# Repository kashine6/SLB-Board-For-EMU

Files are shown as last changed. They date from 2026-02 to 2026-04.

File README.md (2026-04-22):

# SLB-Board-For-EMU

**The mass-produced boards is now available on AliExpress.**

 [Aliexpress](https://www.aliexpress.com//item/1005012025112049.html)

**⚠️ WARNING ⚠️**

Incorrect operations such as reversing the 24V/GND 🔌 or causing a short circuit ⚡ may damage the board. Since EMU uses multiple boards in series 🔗, please carefully ensure that all wiring is correct ☑️.

## Table of Contents

- [Introduction](#introduction)
- [1. PIN Diagram](#1-pin-diagram)
- [2. EMU Wiring Diagram](#2-emu-wiring-diagram)
- [3. EMU Configuration](#3-emu-configuration)
- [4. User Guide for EMU](#4-user-guide-for-emu)
- [5. Flashing Guide (Optional)](#5-flashing-guide-optional)
  - [5.1. Flashing Katapult (Optional)](#51-flashing-katapult-optional)
  - [5.2. Compiling Klipper Firmware](#52-compiling-klipper-firmware)
  - [5.3. Updating Firmware via Katapult](#53-updating-firmware-via-katapult)
  - [5.4. Updating Firmware via DFU](#54-updating-firmware-via-dfu)

---

## Introduction
**SLB (Solo Lane Board)** is a control board designed specifically for **EMU**-style MMU systems, where each lane is driven by an independent controller board.  

No WAGO connectors and no LED daisy-chaining. Supports power and CANBUS cascading, and is compatible with the EMU_Hatch_Board, greatly simplifying EMU wiring.

**Notice:** Maximum rated current for SLB is 8A. If you plan to use PTC drying, only one unit can be operated at a time. For more than one unit, please use WAGO terminals to connect the power supply in parallel.

The SLB is not only suitable for EMU, but can also provide additional channel expansion for systems such as BoxTurtle. The board itself includes built-in support for controlling N20 motors.

This board is factory-produced using high-quality electronic components with SMT assembly, ensuring reliable and consistent quality.

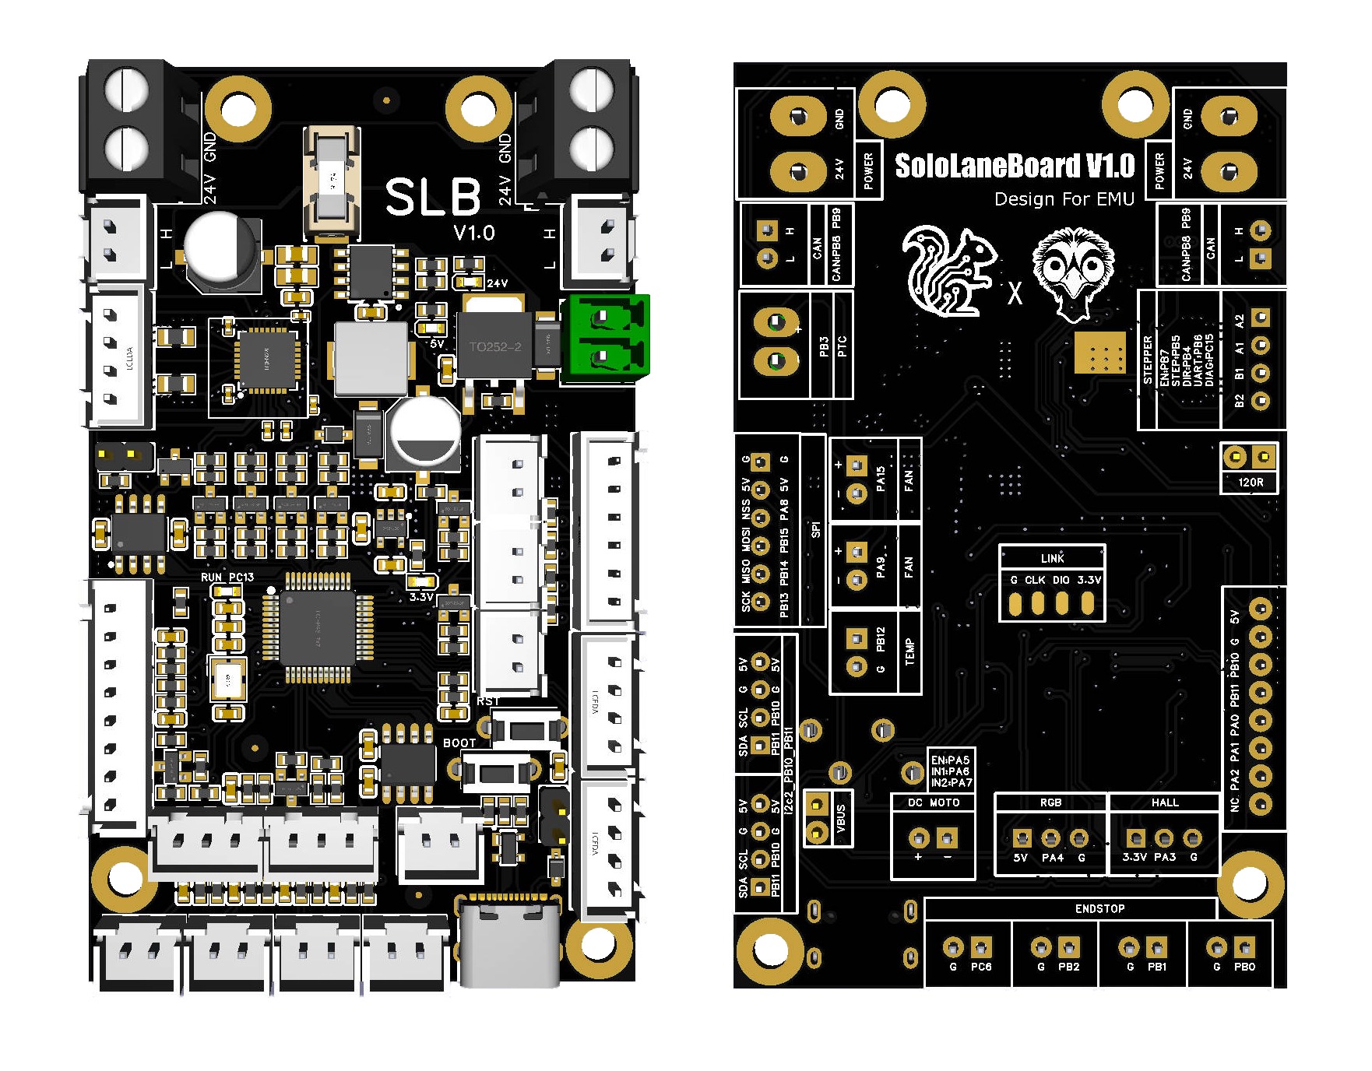
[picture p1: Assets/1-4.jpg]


**It has the following features:**

- **Main Chip**: STM32G0B1CBT6 MCU.
- **Dual power connectors and dual CAN interfaces** for convenient daisy-chaining.
- **1 x Onboard TMC2209** operating in UART mode, with 5V logic circuitry.
- **1x 8-pin XH2.54 connector** is provided for direct connection to the **EMU Hatch Board**.
- **2 × Neo pixel RGB interfaces**, one of which is integrated into the 8-pin XH2.54 connector.
- **6 × I/O connectors**, two of which are integrated into the 8-pin XH2.54 connector.
- **3 × Hardware I2C interfaces**, one of which is integrated into the 8-pin XH2.54 connector.
- **2 × 24V fans** with adjustable speed control
- **1 × PTC heating interface**, 5A max
- **1 × NTC temperature sensor** interface for temperature monitoring
- **1 x Hall ADC interfaces** for PSF Sensor
- **1 x 5V Brushed DC motor drivers** with forward/reverse support, En pin, and sleep mode, support hardware PWM.
- **1 x Hardware SPI interfaces**

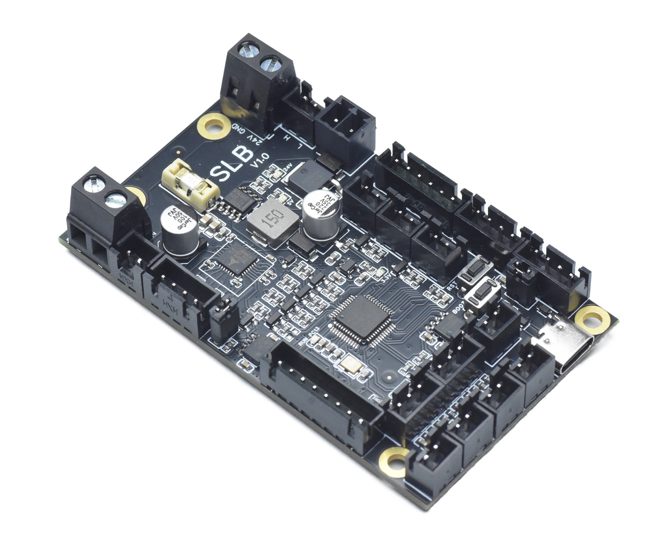
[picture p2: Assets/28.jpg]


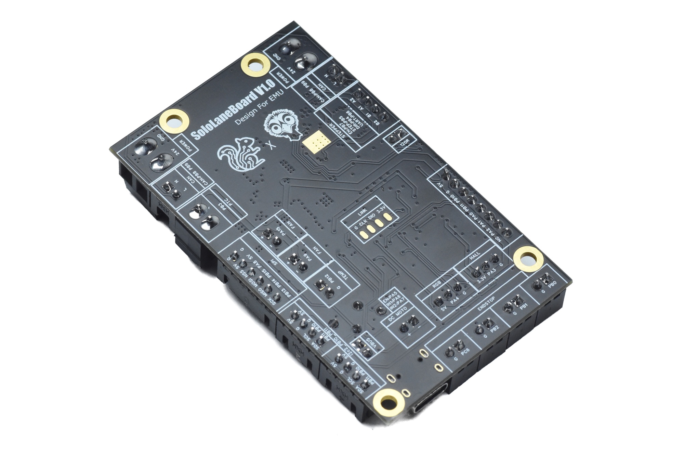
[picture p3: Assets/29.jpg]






## 1. PIN Diagram

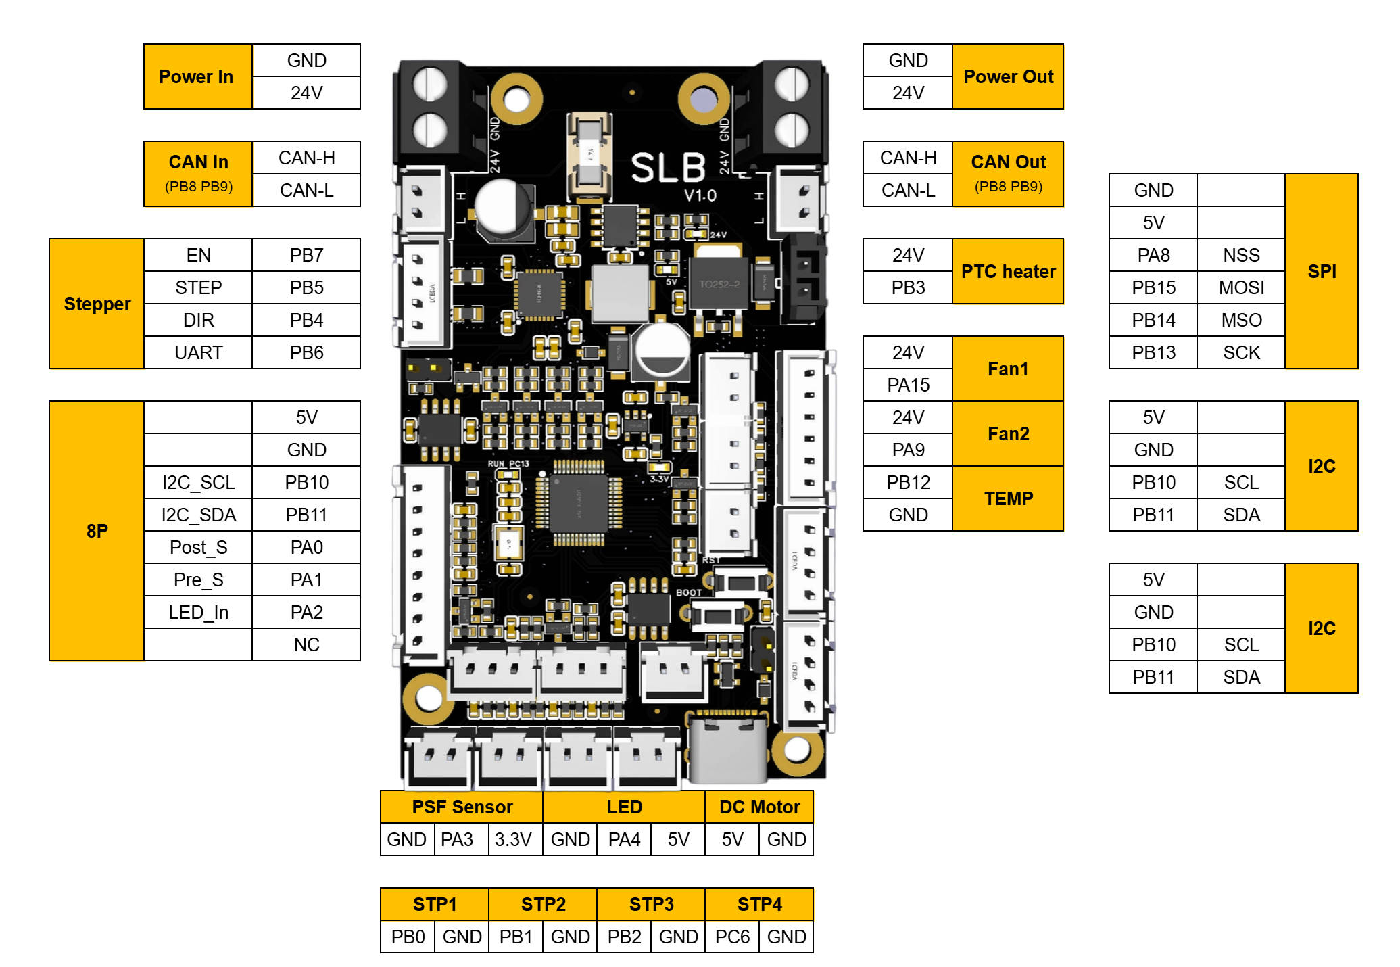
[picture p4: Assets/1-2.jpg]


## 2. EMU Wiring Diagram

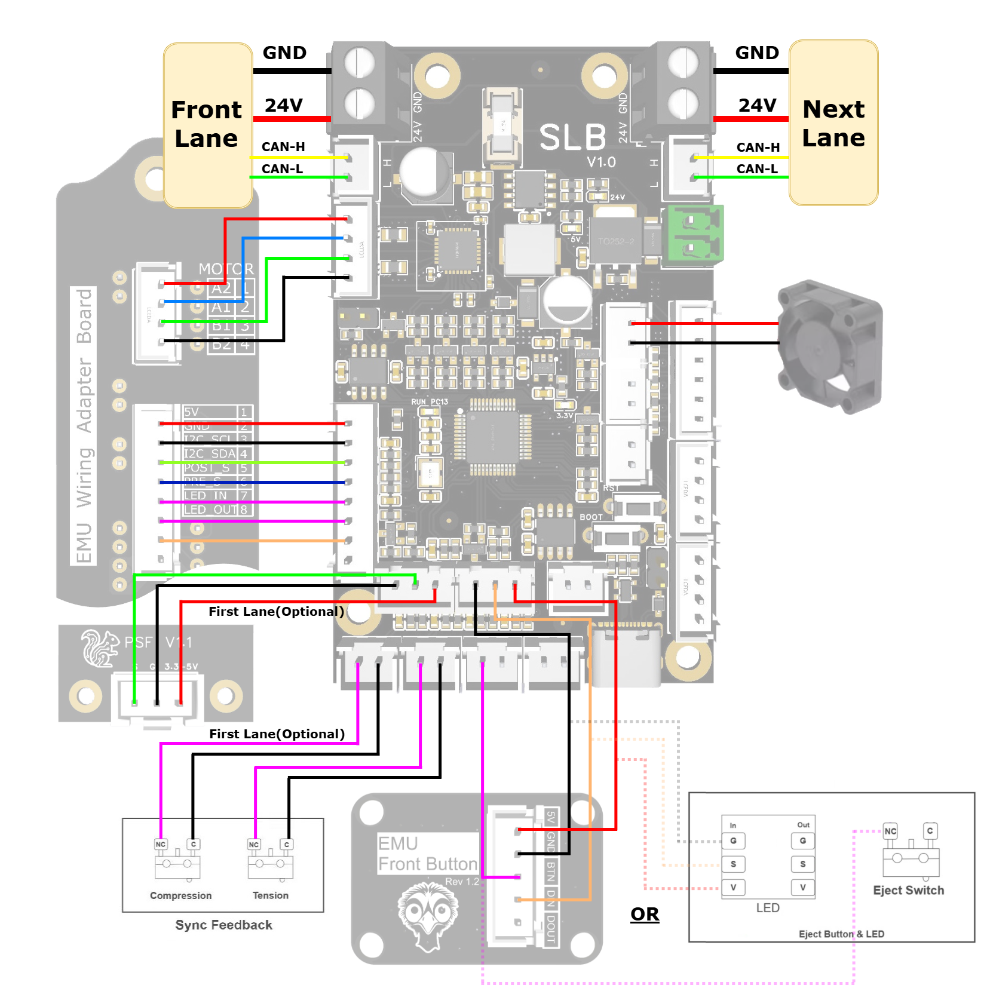
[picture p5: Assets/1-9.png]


For detailed wiring information, please refer to the official EMU documentation:

https://github.com/DW-Tas/EMU/tree/main/docs/assembly_wiring/#solo-lane-board-slb-wiring-dimensions

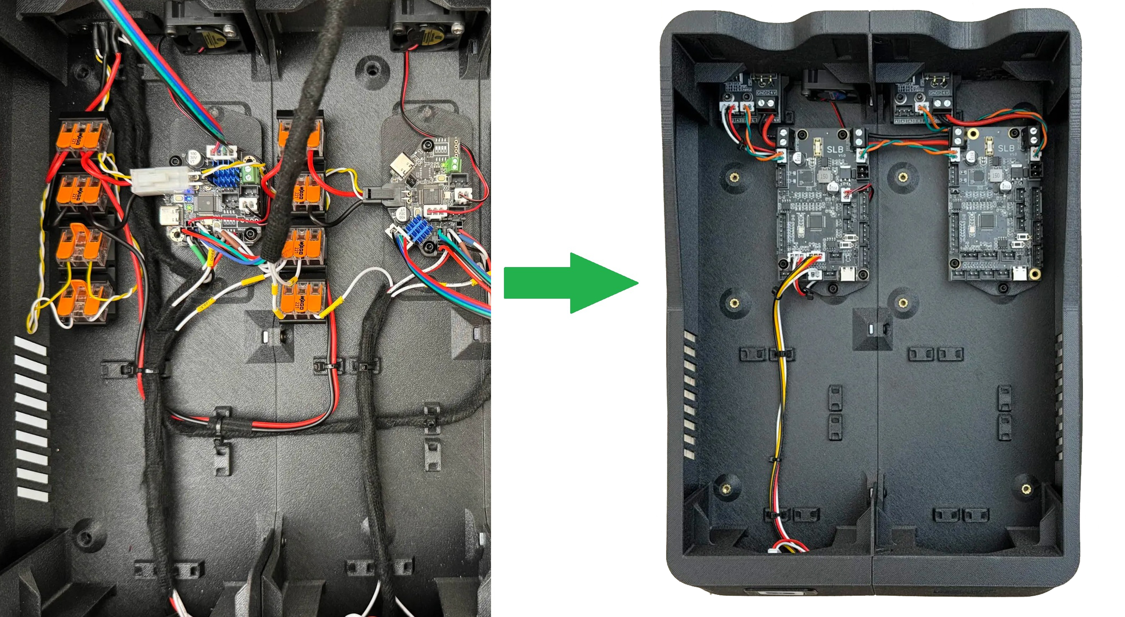
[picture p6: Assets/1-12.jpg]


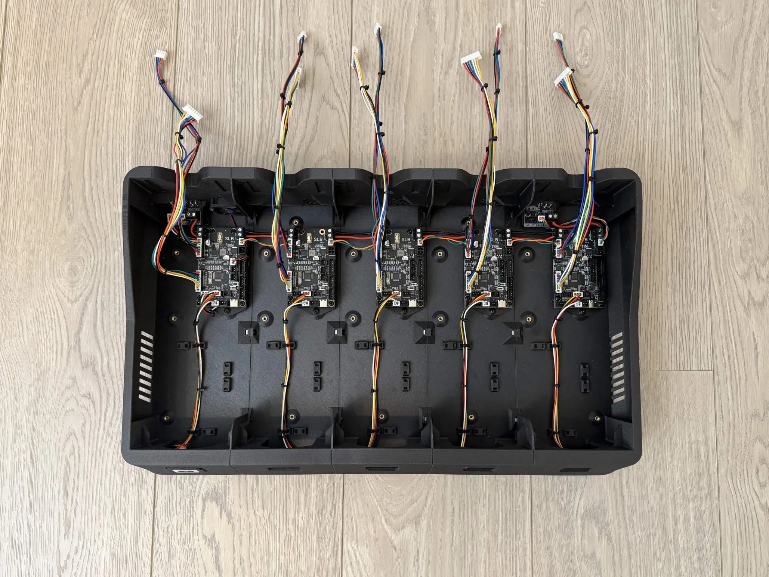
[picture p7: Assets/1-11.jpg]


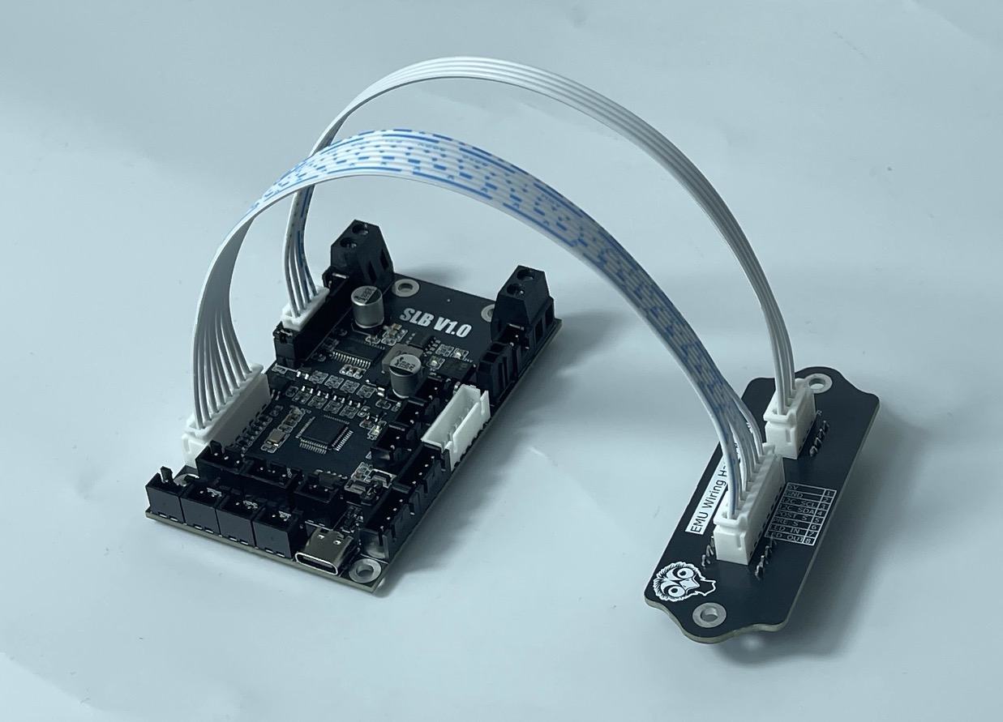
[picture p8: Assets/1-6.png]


**Note:** The wiring harness is for demonstration purposes only. Standard ribbon cables are relatively stiff; you may use silicone ribbon cables or regular loose wires instead.

## 3. EMU Configuration

Please refer to the official EMU documentation:

https://github.com/DW-Tas/EMU/blob/main/docs/software_setup/02-happy-hare-setup.md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

## 4. User Guide for EMU

🟦Has the firmware been flashed

> The **Katapult + Klipper** firmware has already been flashed before shipping, and the CANBUS speed is 1,000,000. So in normal cases, there is no need to reflash.  

🟦About How to use

> You can mount it directly onto the EMU. Note that you may need to remove most of the `120Ω jumpers` on the SLB board (usually keeping only the last one). When the system is unpowered, make sure to use a multimeter to measure the resistance between CAN-H and CAN-L, which should be 60Ω.

🟦How to find the UUID

>Start from the first lane (lane0). Double-click the reset button, then use the command below to find all UUIDs. The UUID shown as “canboot” is the UUID of the current lane. Press the reset button once again; at this point, you will find that the UUID marked as “canboot” is no longer displayed. Then continue the same procedure for the next lane.

``` 
~/klippy-env/bin/python ~/klipper/scripts/canbus_query.py can0
```

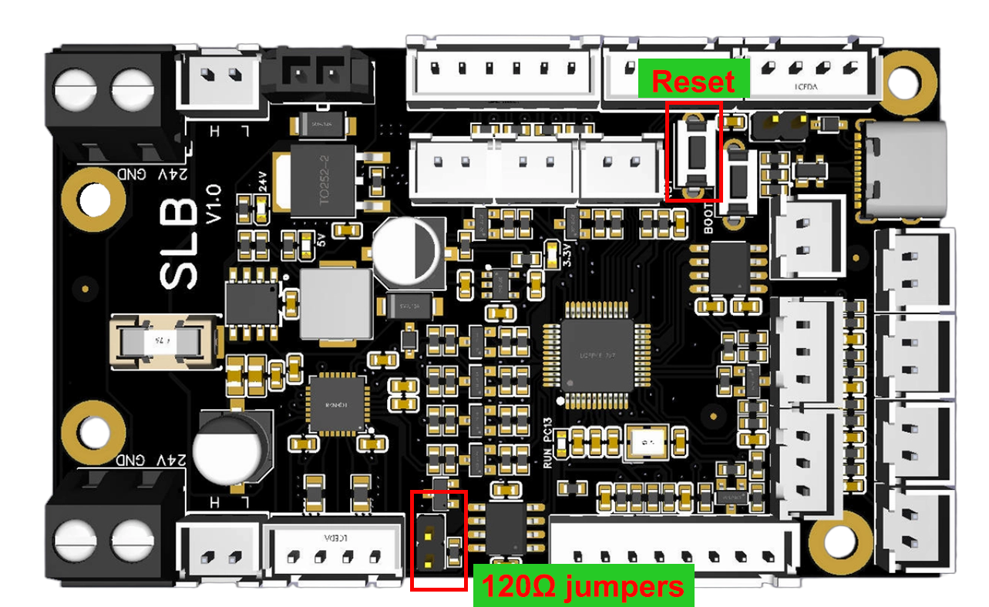
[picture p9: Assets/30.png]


## 5. Flashing Guide (Optional)

> [!TIP]  
>
> The **Katapult + Klipper** firmware has already been flashed before shipping, and the CANBUS speed is 1,000,000. So in normal cases, there is no need to reflash.  
>
> If it is really necessary, you can directly refer to **section 5.3** to upgrade the Klipper firmware using Katapult.

### 5.1 Flashing Katapult (Optional)

Users who only use a CAN connection and want the convenience of quick firmware updates by pressing the Reset button can choose to flash Katapult (formerly known as Canboot).

Katapult is not mandatory, regardless of whether you use a CAN or USB connection.

```bash
# Go to the home directory
cd ~
 
# Download katapult (skip if you already have it)
git clone https://github.com/Arksine/katapult
 
# Enter the katapult directory
cd katapult
```

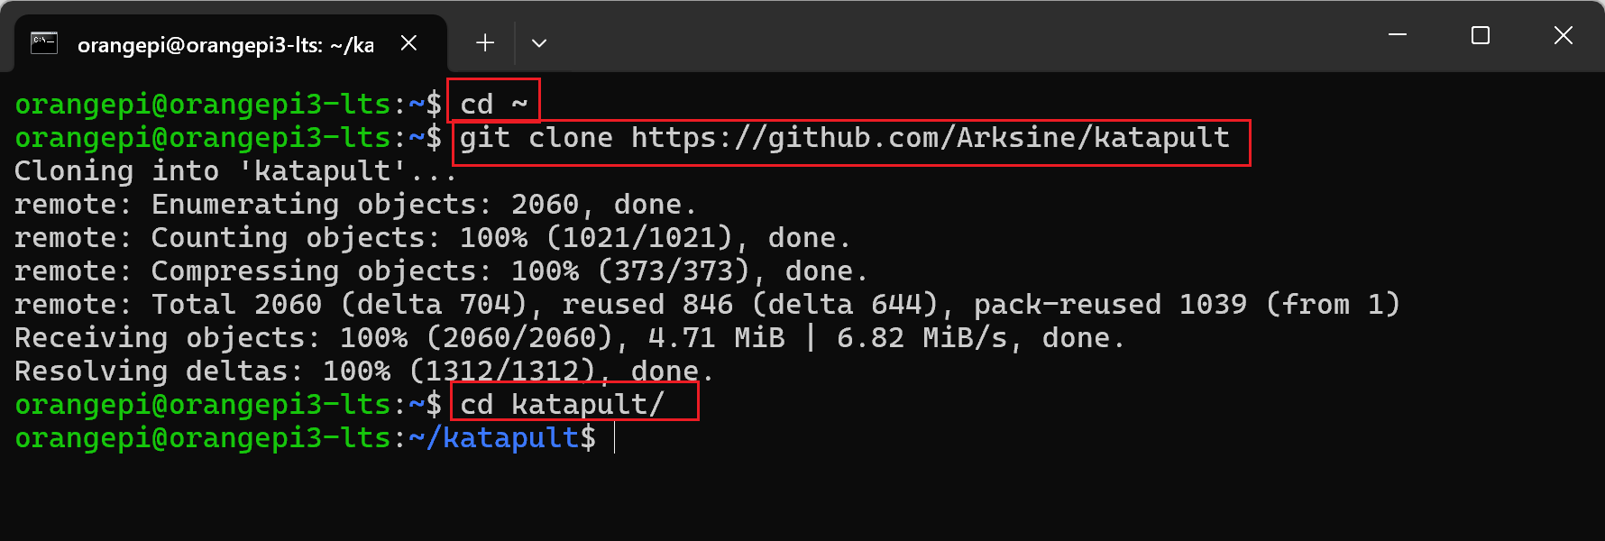
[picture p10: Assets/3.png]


```bash
# Clean the previous build
make clean
 
# Modify the build configuration, fill in the parameters as shown in the image below
make menuconfig
 
# After verifying the settings, press q to exit, select y, then type make to start compiling
make
```

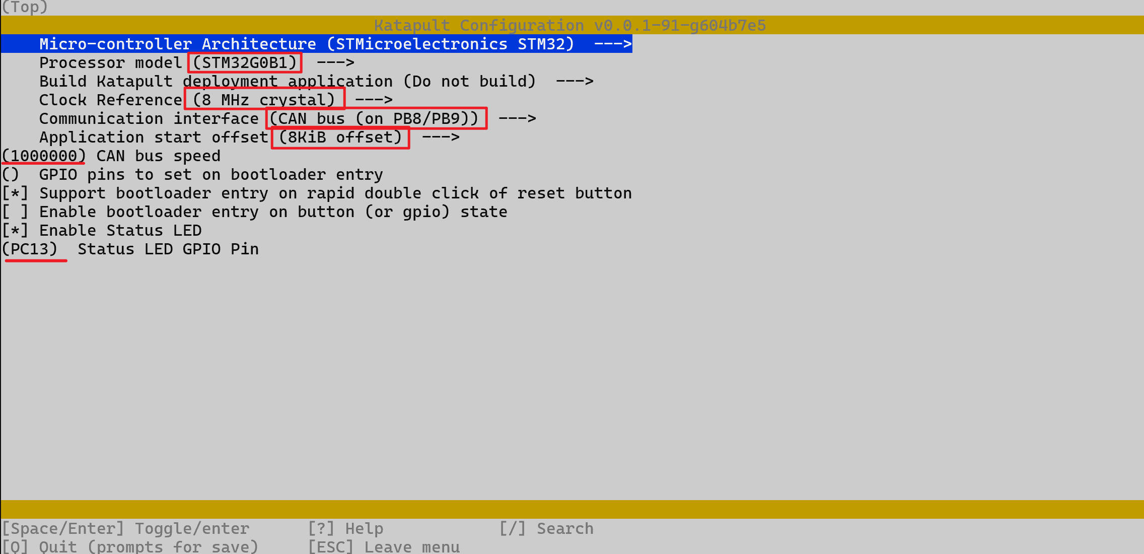
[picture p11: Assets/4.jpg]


> [!TIP]
> The speed can be set according to your needs, 1000000 is recommended.

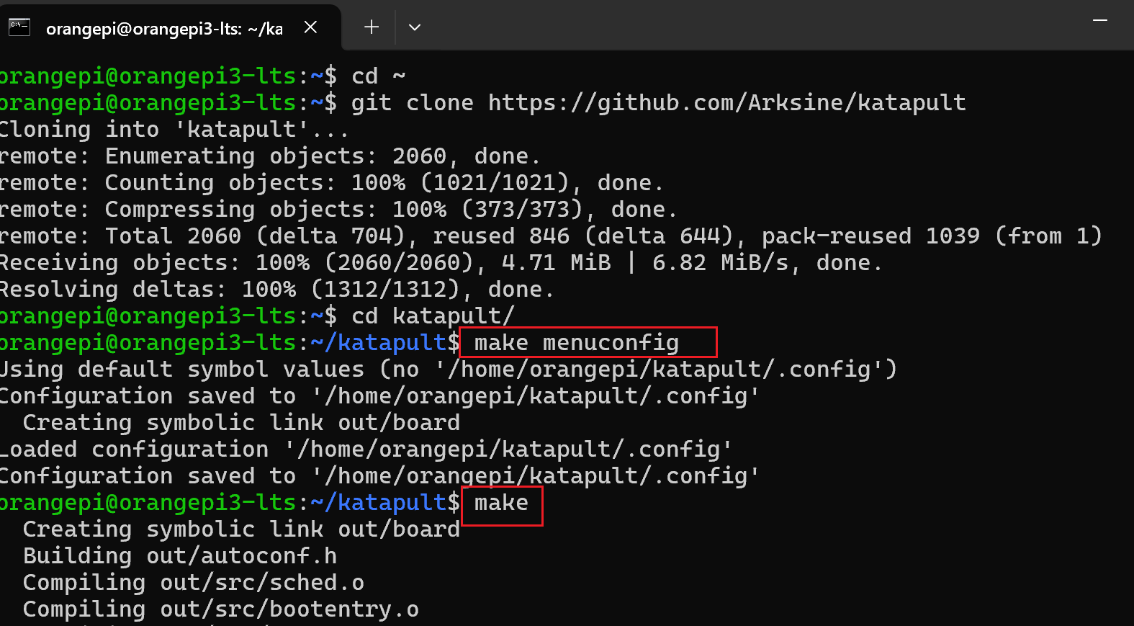
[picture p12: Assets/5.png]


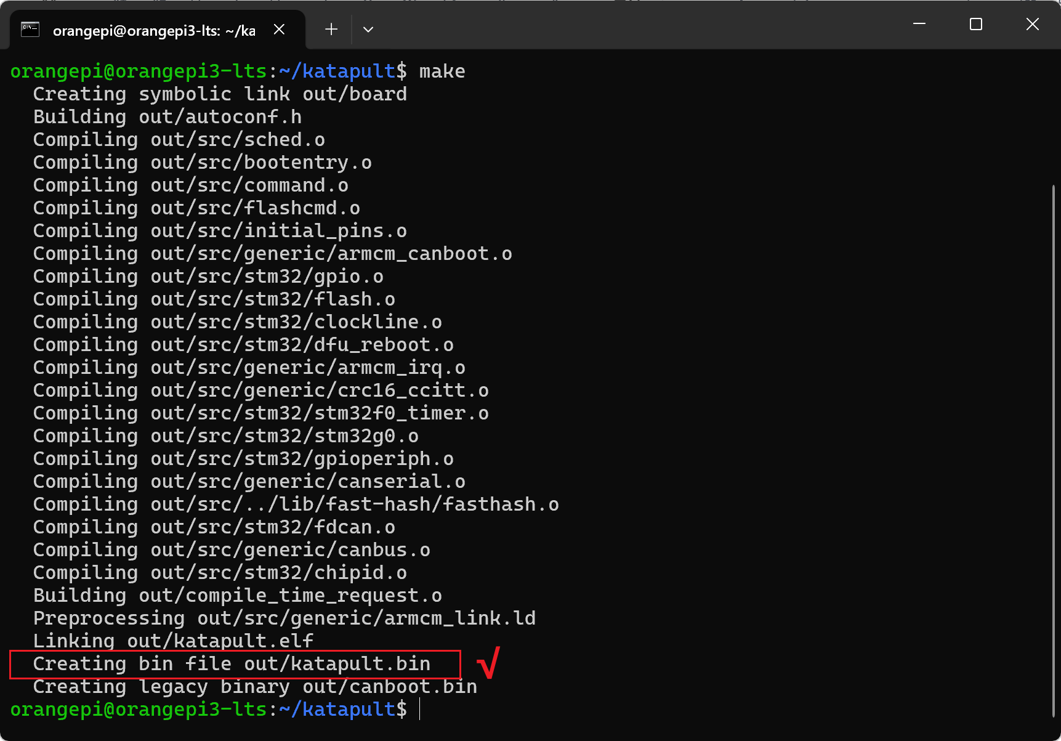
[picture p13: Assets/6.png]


After compilation, katapult.bin will be generated in the ~/katapult/out folder.

**Entering DFU Mode**

Use a jumper to short the 5V USB pins. After shorting, you can power the board via USB for flashing. 

> [!TIP]
> Remember to remove the jumper after flashing is complete.  

If you are using 24V to power the board, you do not need to short the jumper, but you can only use Method 2 below to enter DFU mode.

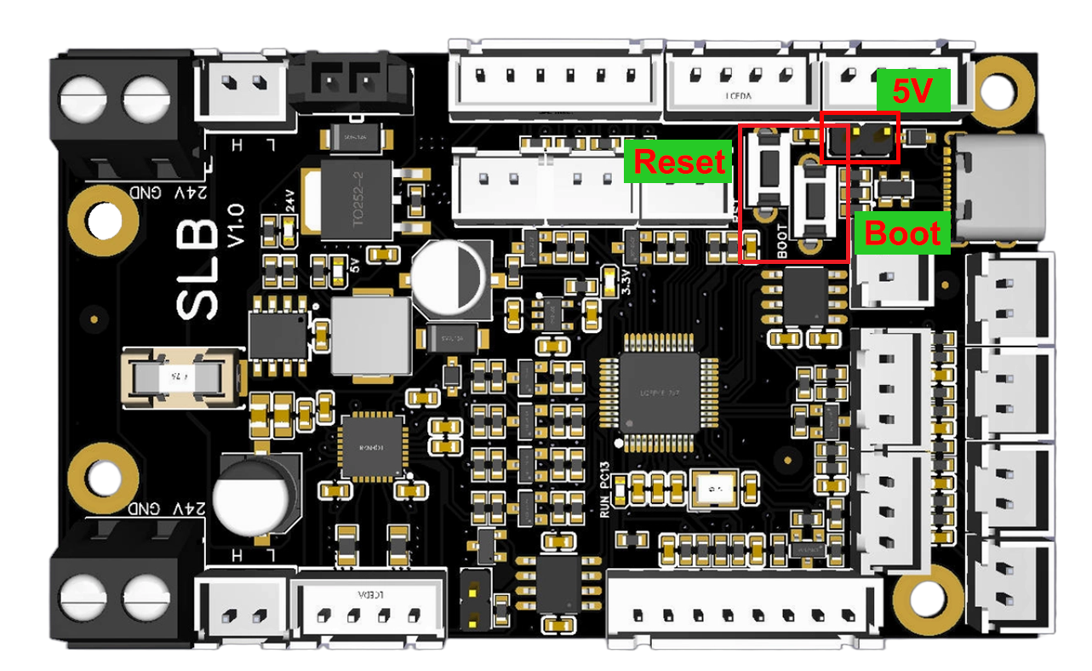
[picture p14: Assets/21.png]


- **Method 1 to enter DFU:** With the board completely powered off, press and hold the Boot button, connect the board to the host computer with a Type-C cable, then release the Boot button.

- **Method 2 to enter DFU:** If the board is powered on, connect it to the host computer with a Type-C cable, then press and hold the Boot button, press and release the Reset button, release the Reset button, and finally release the Boot button.

Then use the lsusb command to check if a DFU device is present.

```bash
lsusb
```

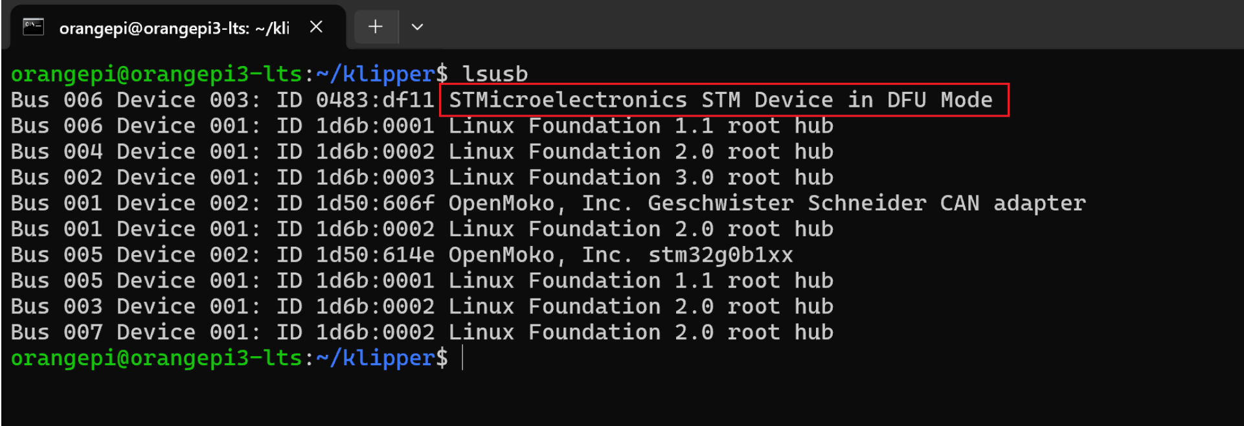
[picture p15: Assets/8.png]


Use the following command to flash the board:

```bash
make flash FLASH_DEVICE=0483:df11
```

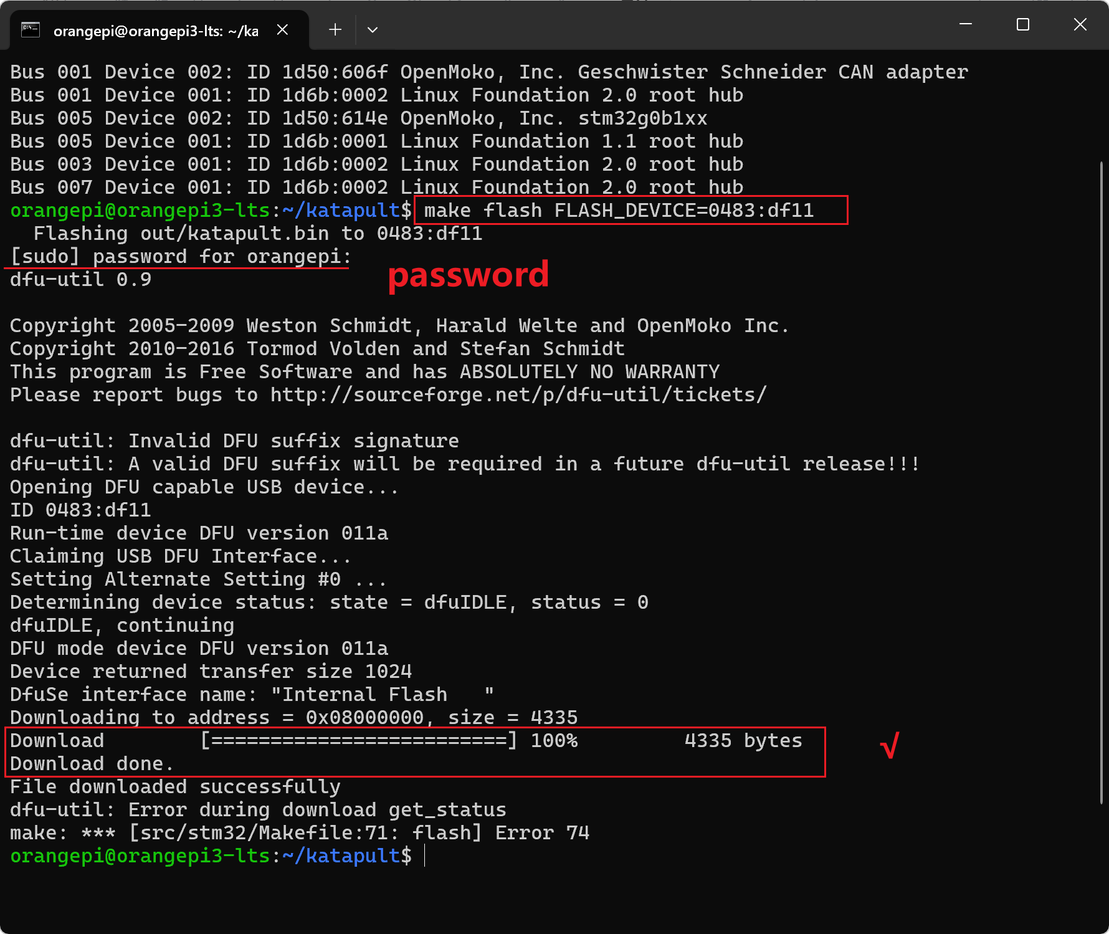
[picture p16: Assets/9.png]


After flashing is complete, please unplug the USB cable and connect the CAN signal cable and 24V power supply.

> [!NOTE]
> 1: Remember to remove the 5V USB jumper.  
> 2: If you have multiple CAN devices, you only need to short the 120-ohm resistor on one device. It is best to short the 120-ohm resistor on the mainboard at the end of the chain.  
> 3: Pay close attention to the wiring order of 24V, GND, CAN-H, and CAN-L. Double-check carefully. Incorrect wiring may cause the mainboard to burn out, and you will be responsible for the consequences.  

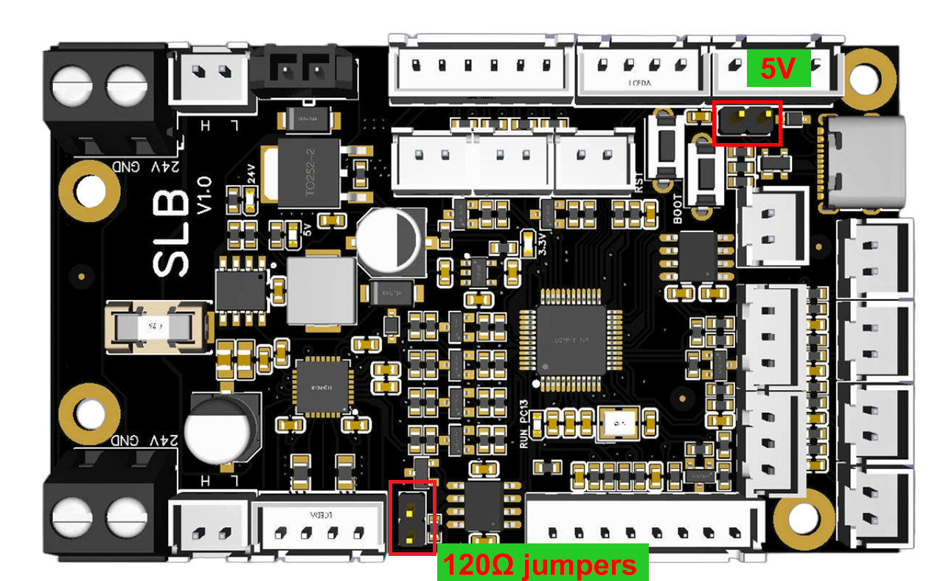
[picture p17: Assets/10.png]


Use the following command to check the CAN UUID. 
> [!TIP]
> You may need to quickly double-press the reset button to enter the bootloader.

```bash
~/klippy-env/bin/python ~/klipper/scripts/canbus_query.py can0
```

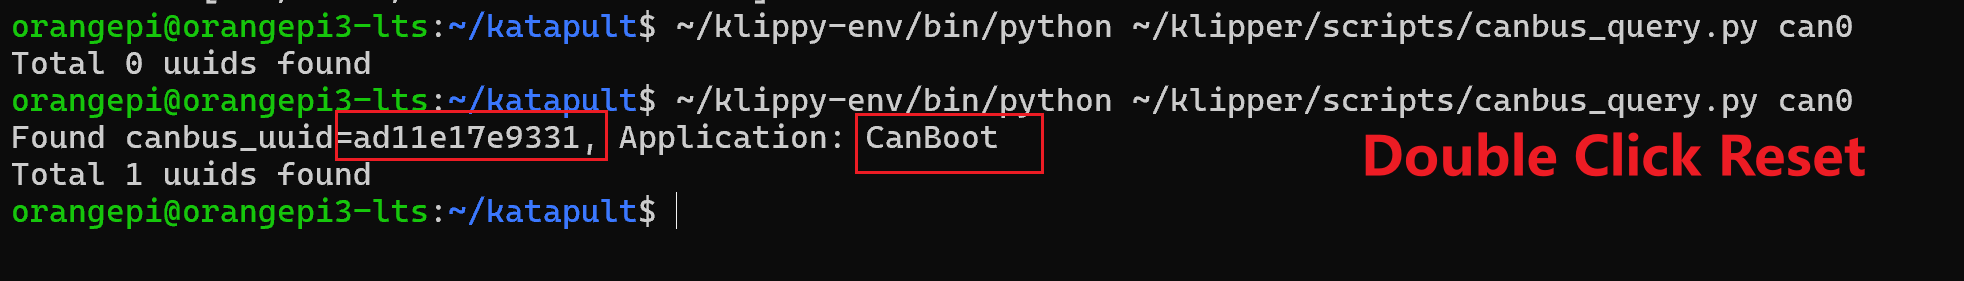
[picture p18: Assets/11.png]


### 5.2 Compiling Klipper Firmware

SSH into your host machine.

```bash
# cd to the klipper directory
cd ~/klipper
 
# Clean the previous build
make clean
 
# Configure the build parameters [refer to the image below]
make menuconfig
```



Set the build parameters according to the protocol you need to use.

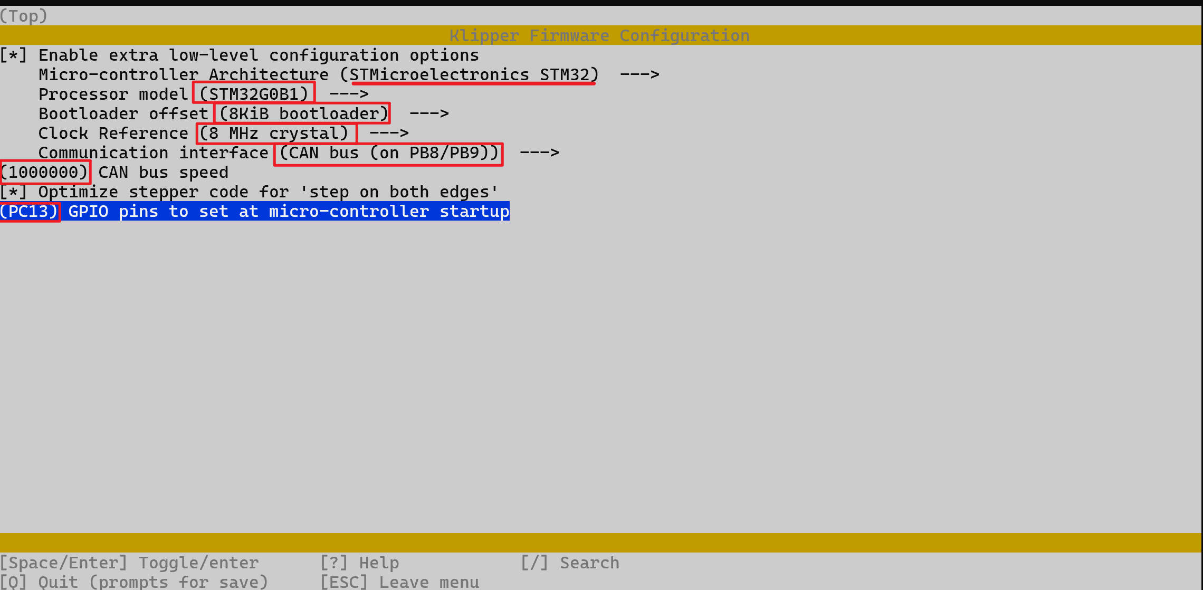
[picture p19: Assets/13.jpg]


```bash
# If not using Katapult
Bootloader offset (No bootloader) --->
 
# If using Katapult
Bootloader offset (8KiB bootloader) --->
 
# If using USB communication via Type-C
Communication interface (USB (on PA11/PA12)) --->
 
# If using CANBus communication
Communication interface (CAN bus (on PB8/PB9)) --->
 (1000000) CAN bus speed
```

Press `q` to exit, and `y` to save.

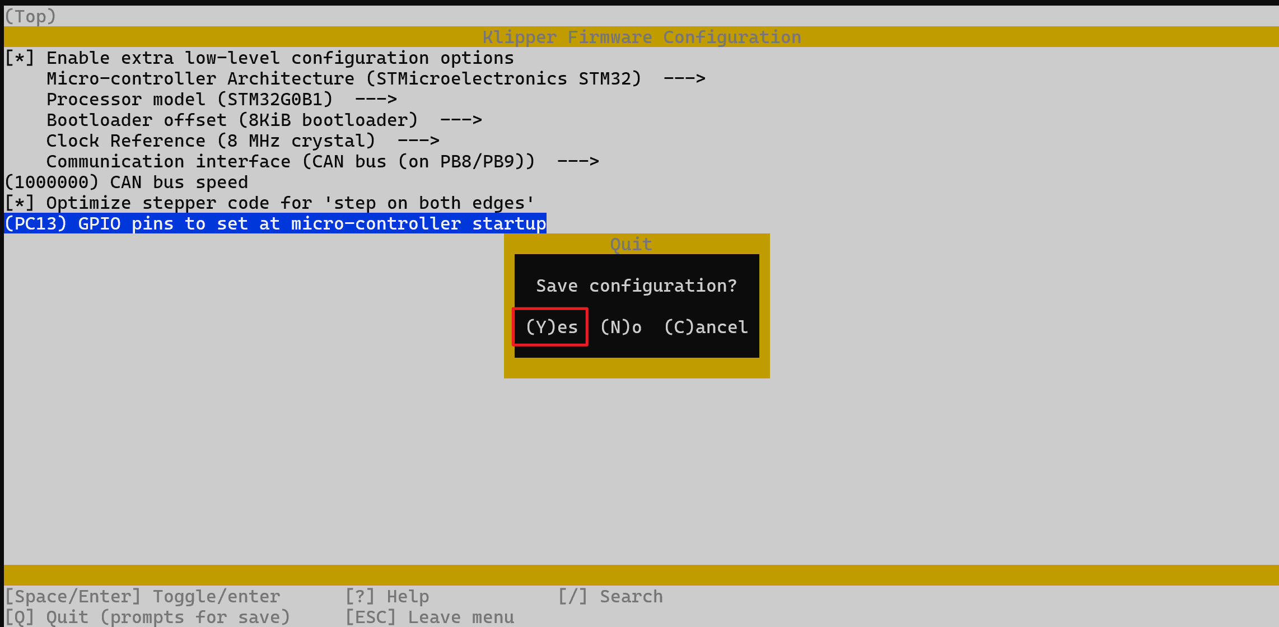
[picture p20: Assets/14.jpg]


Enter the make command to start compiling.

```bash
make
```

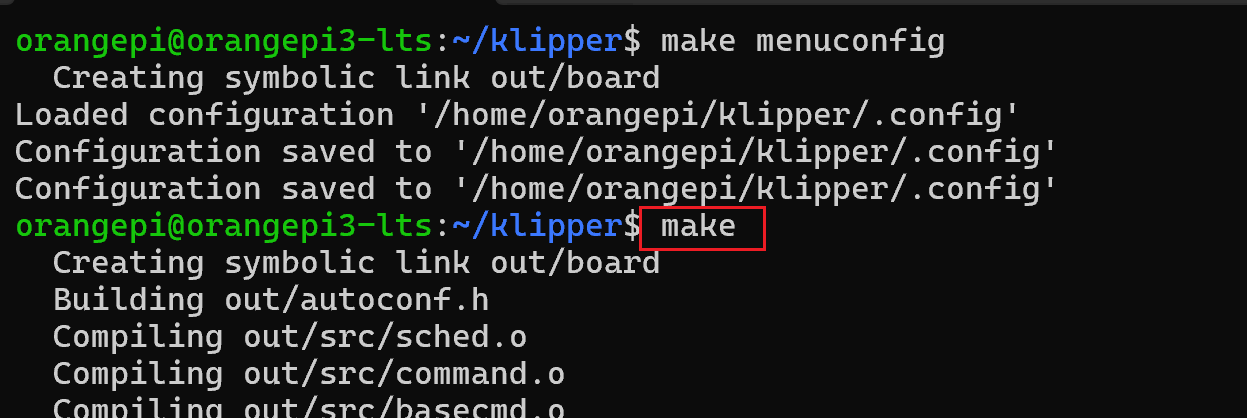
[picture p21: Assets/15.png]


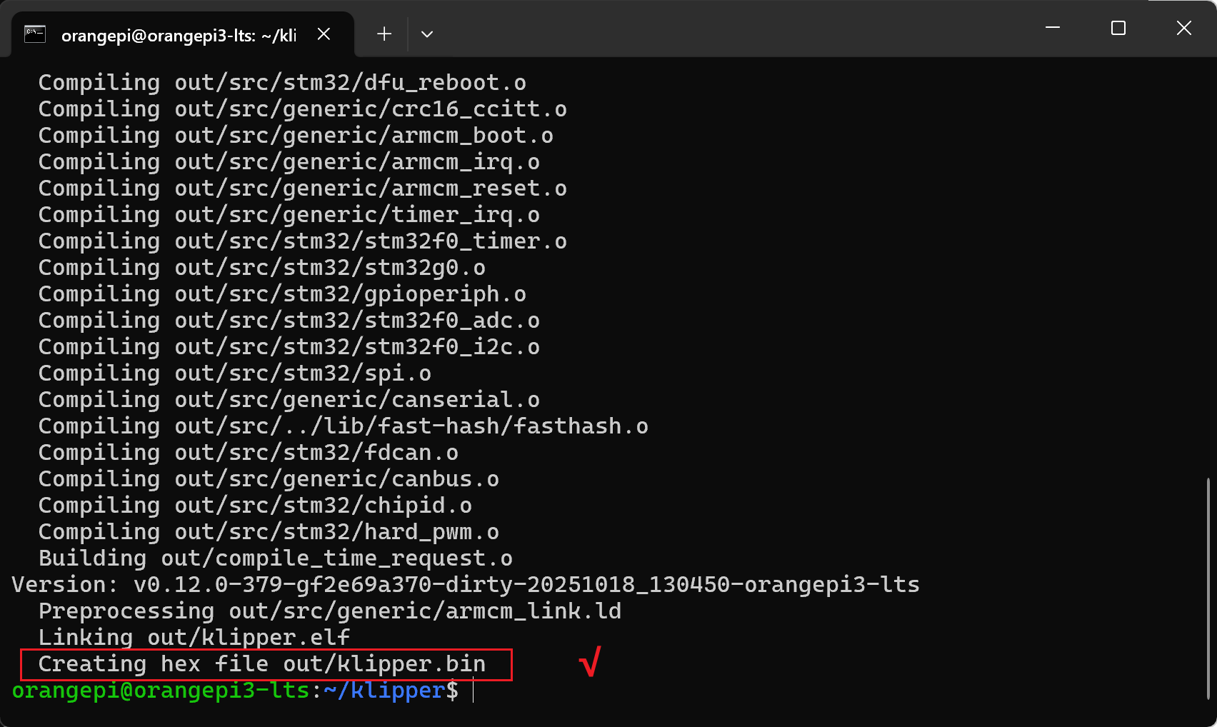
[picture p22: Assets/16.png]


### 5.3 Updating Firmware via Katapult

Connect the CAN signal cable and 24V power supply.

> [!NOTE]
> 1: Remember to remove the 5V USB jumper.  
> 2: If you have multiple CAN devices, you only need to short the 120-ohm resistor on one device.  
> 3: Pay close attention to the wiring order of 24V, GND, CAN-H, and CAN-L. Double-check carefully. Incorrect wiring may cause the mainboard to burn out, and you will be responsible for the consequences.  



Then use the following command to check the UUID:

```bash
~/klippy-env/bin/python ~/klipper/scripts/canbus_query.py can0
```

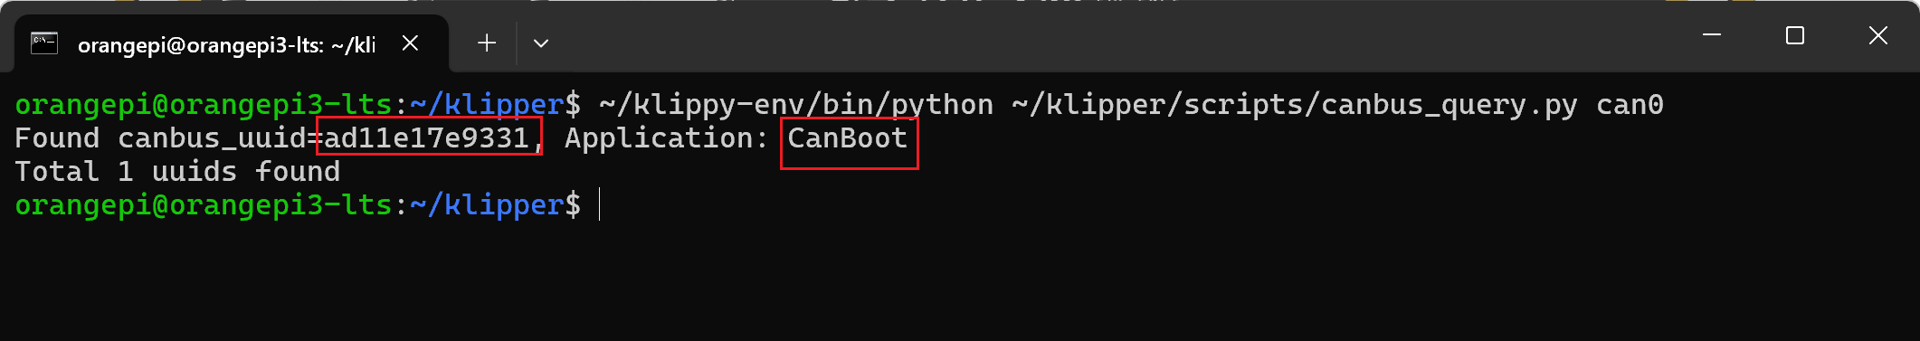
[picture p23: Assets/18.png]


Use the following command to flash in CAN mode:

```bash
cd ~/katapult/scripts
 
python3 flashtool.py -i can0 -f ~/klipper/out/klipper.bin -u your_uuid_here
```

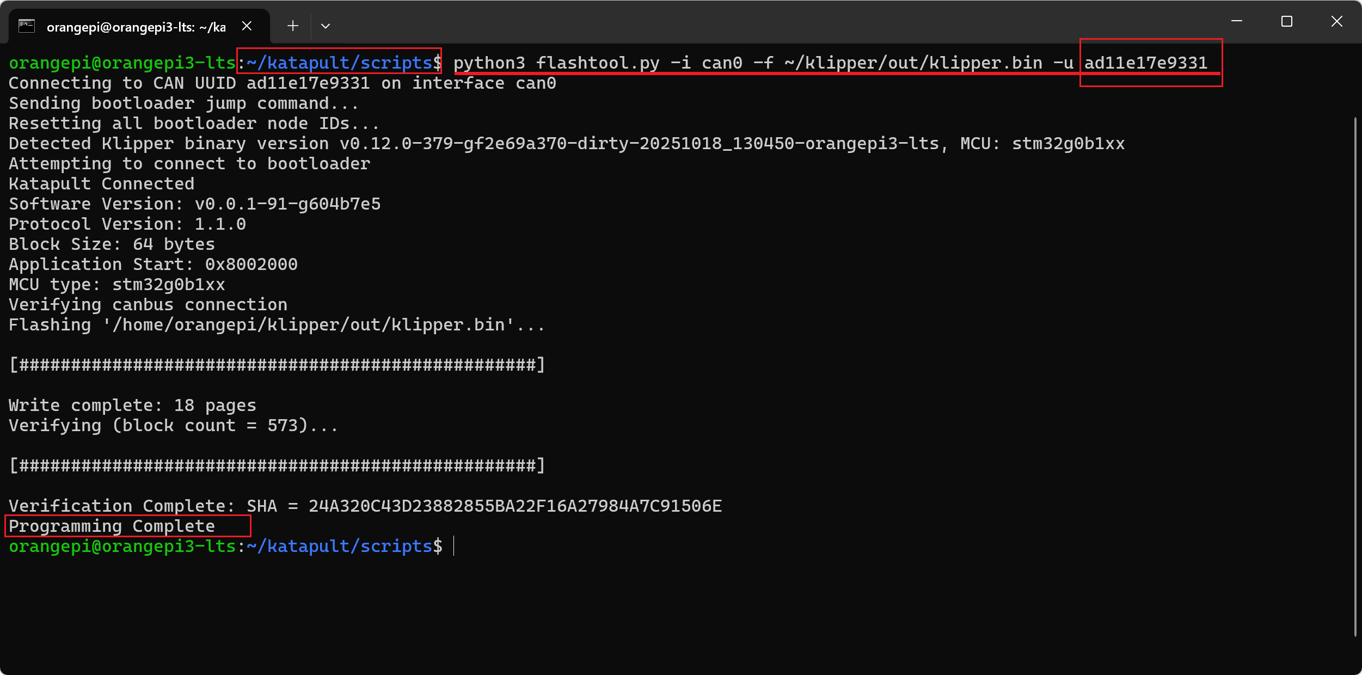
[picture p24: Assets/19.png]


Then continue to use the previous command to check the CAN information.



> [!TIP]
> To upgrade the CAN firmware in the future, repeat this process. When compiling the Katapult firmware earlier, we set it to enter Katapult mode by double-pressing the reset button. 
> In practice, you can also directly enter the flashing command, and the board will automatically restart and enter Katapult.  

### 5.4 Updating Firmware via DFU

1: Enter DFU mode.

Use a jumper to short the 5V USB pins. After shorting, you can power the board via USB for flashing. 

> [!TIP]
> Remember to remove the jumper after flashing is complete.

If you are using 24V to power the board, you do not need to short the jumper, but you can only use Method 2 below to enter DFU mode.



- Method 1 to enter DFU: With the board completely powered off, press and hold the Boot button, connect the board to the host computer with a Type-C cable, then release the Boot button.

- Method 2 to enter DFU: If the board is powered on, connect it to the host computer with a Type-C cable, then press and hold the Boot button, press and release the Reset button, release the Reset button, and finally release the Boot button.

2: In SSH, type lsusb to check if a DFU device appears. Normally, a DFU device should appear.

If no DFU device appears, repeat the operation.

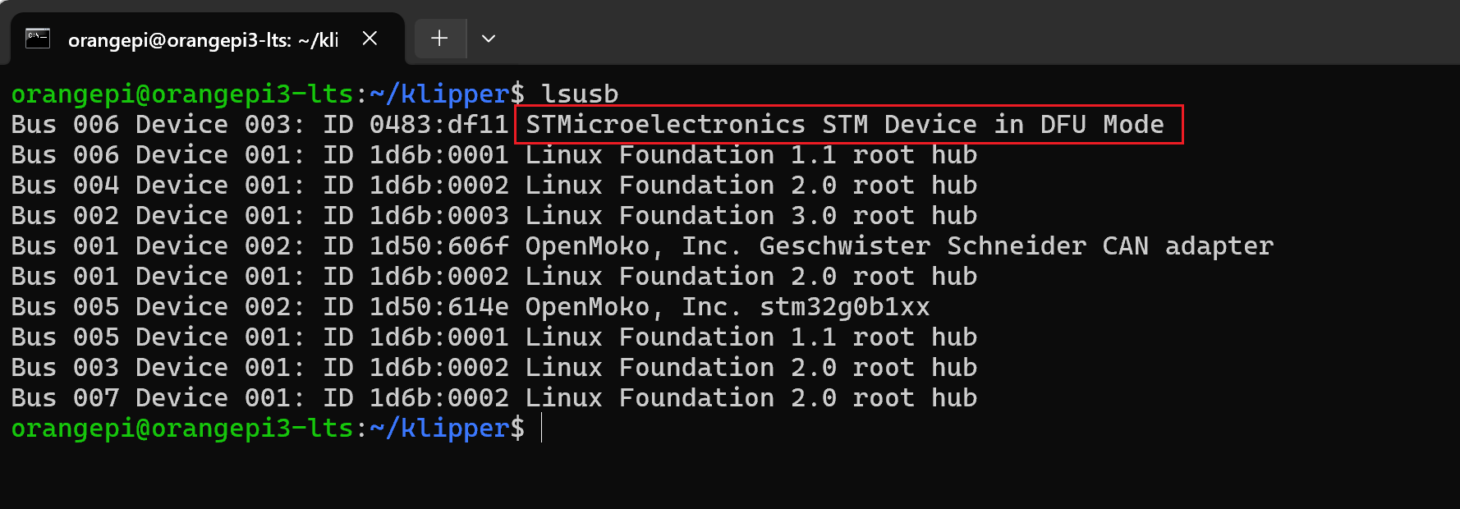
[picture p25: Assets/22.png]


3: In SSH, enter:

```bash
# Make sure you are in the klipper directory
cd ~/klipper
 
# 0483:df11 is the ID found with lsusb earlier
# If it says make not found, install it with sudo apt install dfu-util -y
 
make flash FLASH_DEVICE=0483:df11
```

The flashing process will then begin [you may need to enter your password]. Wait for the progress bar to complete. When "successfully" appears, it means the flashing was successful.

You can ignore any errors that appear after "successfully".

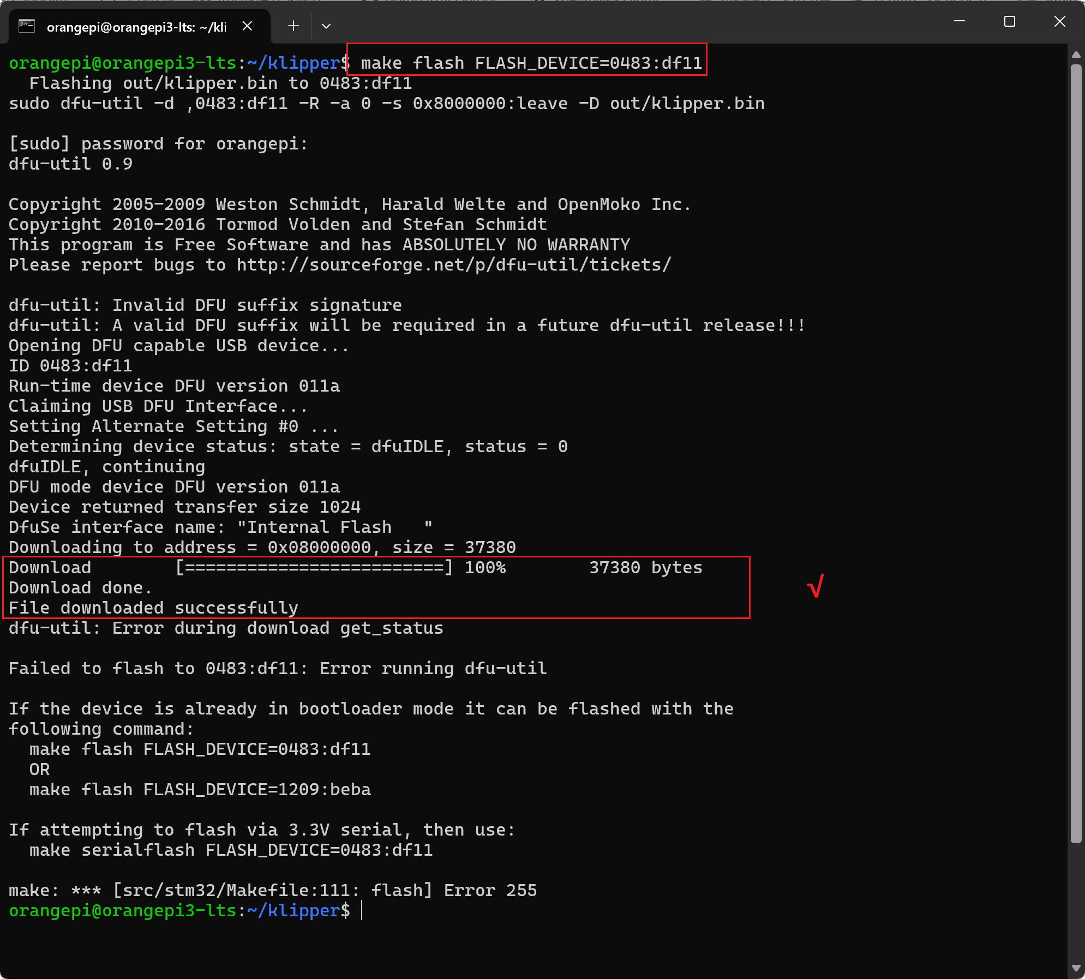
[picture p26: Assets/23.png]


Flashing is complete.

4: **Get the serial ID**

Unplug and replug the USB data cable, use lsusb to check if there is an stm32f446 device.

Use the following command to check the device's serial ID:

```bash
ls /dev/serial/by-id/
```



The serial ID for this device is:

```bash
serial: /dev/serial/by-id/usb-Klipper_stm32g0b1xx_20003A00025030544E383020-if00
```

> [!TIP]
> For later use, please remove the 5V USB jumper and connect 24V power to the CAN interface.

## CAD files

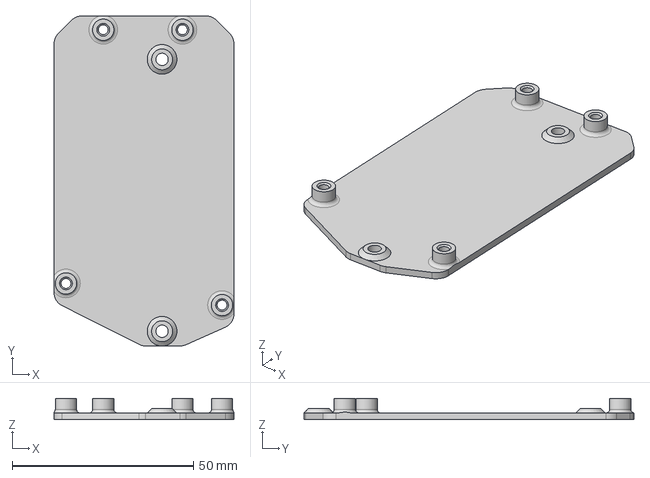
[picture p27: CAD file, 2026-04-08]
STLS/CAD/[a]_SLB_Mount_for_EMU.step
49.6 x 91.0 x 5.80 mm

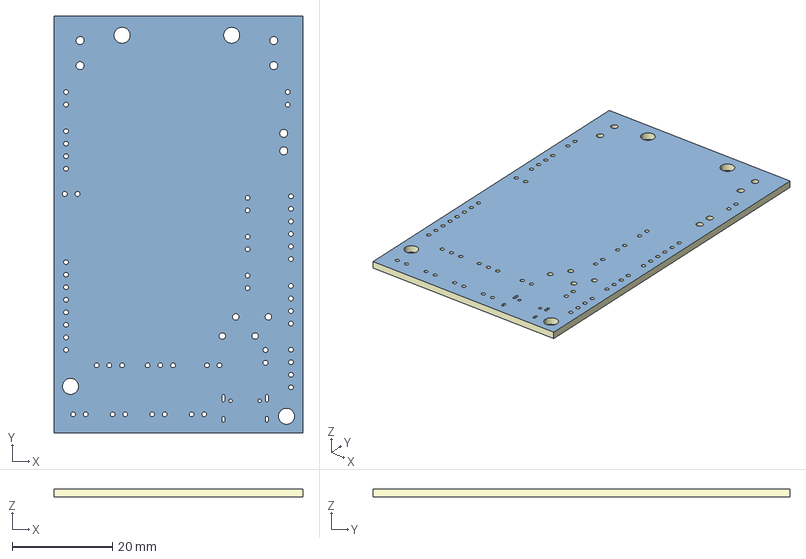
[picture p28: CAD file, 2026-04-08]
STLS/CAD/SLB_3D_PCB_2026-04-08.step
49.6 x 83.0 x 1.60 mm
Board~bP3G
TopCopper~bP3G
BottomCopper~bP3G
TopFpcStiffener~bP3G
BottomFpcStiffener~bP3G

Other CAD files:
STLS/[a]_SLB_Mount_for_EMU.stl
